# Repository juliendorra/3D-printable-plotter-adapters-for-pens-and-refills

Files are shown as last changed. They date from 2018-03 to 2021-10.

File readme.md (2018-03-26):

# 3D printable plotter adapters for pens and refills

Use your favorite contemporary pens on vintage HP plotters with this parametric OpenSCAD code to create custom adapters.

These adapters allow you to use pens or even directly refills with vintage HP plotters like the HP 7440A, HP 7550A, HP 7475A… and other vintage plotters using the same standard for pens.

This version was created to be quick and simple: **3 measures using a caliper, and in 5 minutes you are ready to print a new adapter** (printing itself will take maximum 20 minutes, depending on your settings and printer).

The goal was to be able to create an adapter for any random pen laying around or newly bought without thinking to much about it, trying and see what works best.

If you are interested in vintage plotters but don't know where to start, here's a list of ressources, manuals, articles, posts and artworks: [https://workflowy.com/s/Cl4.I8zutkIg5K](https://workflowy.com/s/Cl4.I8zutkIg5K)

You can also check the [#plottertwitter hashtag on Twitter](https://twitter.com/hashtag/plottertwitter).

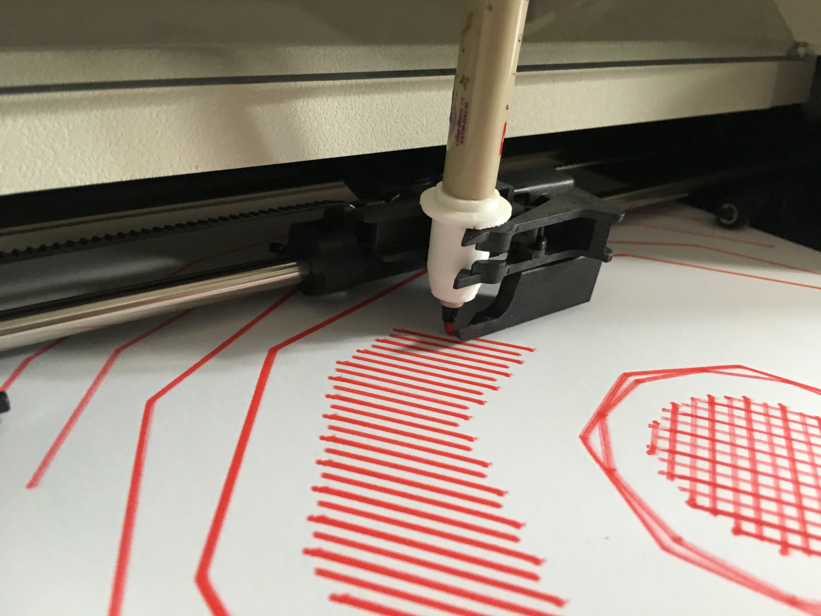
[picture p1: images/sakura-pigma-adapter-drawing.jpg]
sakura-pigma-adapter-drawing

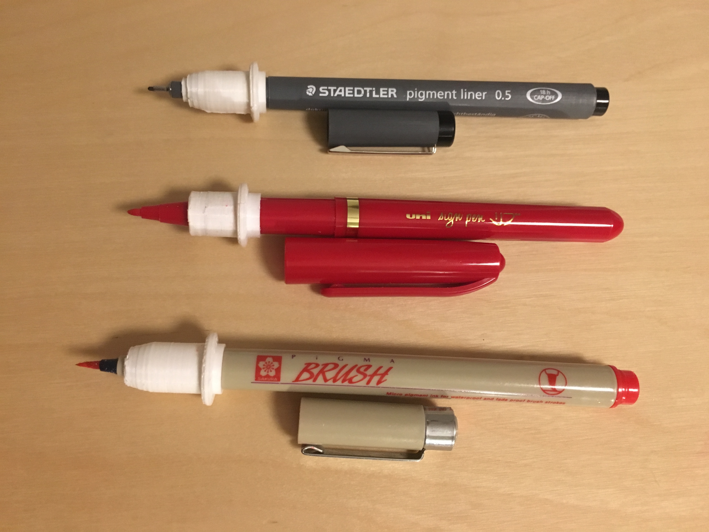
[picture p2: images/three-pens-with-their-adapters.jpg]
three-pens-with-their-adapters


## How to create your own adapter to use your favorite pen on your vintage HP plotter:

- Duplicate one of the existing OpenSCAD adapter files, for example `Staedtler pigment line plotter pen adapter.scad` (note that you'll need to keep the `plotter_pen_adapters_common.scad` file in the same folder as your new file, as it is imported by your adapter code)

- Select a stop-point near the tip of your pen. It is frequently the cap limit, but sometimes it more practical to use another narrowing along the body of the pen.

- Measure the maximum diameter of your pen above and below the chosen stop point, and add them to the `pen_top_diameter` (bigger) and `pen_bottom_diameter` (smaller) parameters.

- Measure the distance from the tip (ie. the paper) to the stop-point, and add that value to `height_where_pen_diameter_change`.

Note: for proper measuring, it is easier and more precise to use a caliper.

Optionnally, you can also adjust :

- `diameter_spacing` Increase to have lower tolerances (more space) and make it easier to slide the pen in and out. Decrease to have higher tolerances (less space) and have a tigher fit for the pen.

- `top_cut_off_height` It can reasonably be adjusted between `total_body_height - 11.5` and `total_body_height - 0` (Full height of the top body. Longer printing time). If you cut below `total_body_height - 11.5` the grip might suffer (to be tested :-)

- `simplified_body_shape` By default, the generator uses a realistic body shape for the adapter outer body, similar to the original HP pens. Add `simplified_body_shape = true ;` to your adapter code to use a simplified cylindrical lower body.  
You **will need** to use the simplified lower body if the `height_where_pen_diameter_change` value for your stop point is low, close to the paper as with the Edding calligraphy pens, and/or if the `pen_bottom_diameter` value is high, the pen being wide at the tip. In this cases the realistic body is not wide enough to allow for substracting the lower cylinder, cutting the adapter short or creating a hole in it.  
The downside of using the simplified body is that the adapter will no longer fit in a pen plotter rack or carrousel.

## 3D Printing

The printing shouldn't take more than 20 minutes, maybe less with a better printer that the low-cost (300€!) printer that was used to print the first adapters.

The main obstacle to properly printing these adapters is the flange (or band) around the adapter's body, which overhang.

You might very well be able to print it without support, but the first test were nicely successful by using the supports generated by Slic3r Prusa Edition (**not** on an Original Prusa i3). The supports were easy to remove, didn't add too much time and helped get a functionnal print.

You can use a very low infill. The first adapters were printed with a 10% cubic infill and are strong enough.

## This is based off:

- [Code from Sasha Kovar from a design by Brian Boucheron](https://www.thingiverse.com/thing:1261805/)
- [Code and measurements by Ed Nisley KE4ZNU April 2015](https://softsolder.com/2015/04/21/hp-7475a-plotter-oem-pen-body-model/) 

It differs and merge them in the following ways:

- the whole plotter HP pen model from Ed Nisley is used as a base. 
- then we substracts two cylinders. They are used as empty space for the target pen.
- The bottom cylinder is meant to be smaller than the top one, as most pens narrow before the tips.
-  The height where the pen diameter change is used as a parametric stop-point, set so the tip of the pen exactly touch the paper. 

It's also inspired by these other projects:

- [Full model of short and long plotter pens OpenSCAD file](https://www.thingiverse.com/thing:227985)

- [Ball pen insert adapter derived from the full models. STL file.](https://www.thingiverse.com/thing:762716)

## To do

- Emboss the reference or name of the pen around the pen adapter to avoid confusion when you have multiple adapters

- Add and test a tilt angle parameter to give a slight fixed angle to the tip when touching the paper. The maximum angle possible would need to be tested to avoid collisions. It might help in using highlighters or other asymetrical tips.

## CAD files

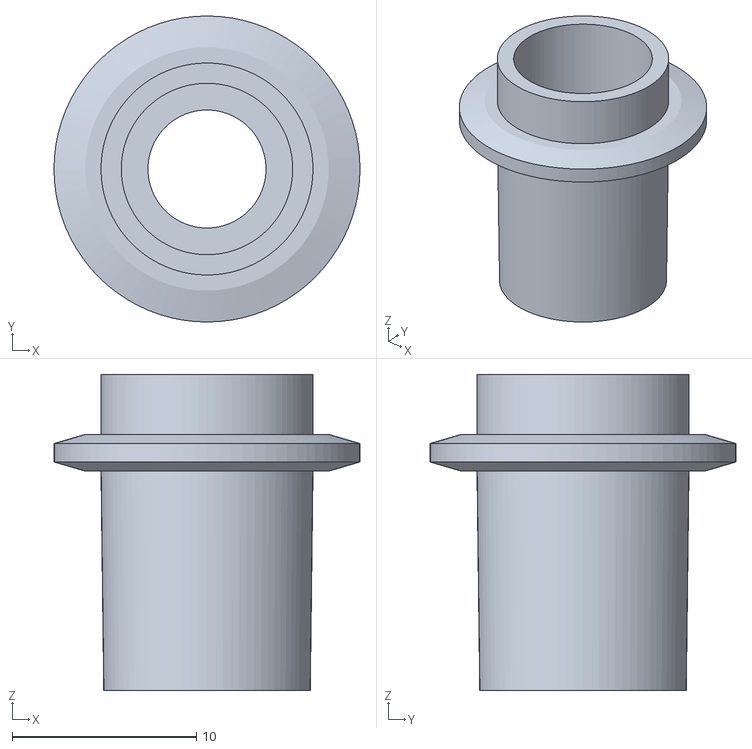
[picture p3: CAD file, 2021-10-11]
DeSerres Mateo plotter pen adapter.stl
16.6 x 16.6 x 17.2

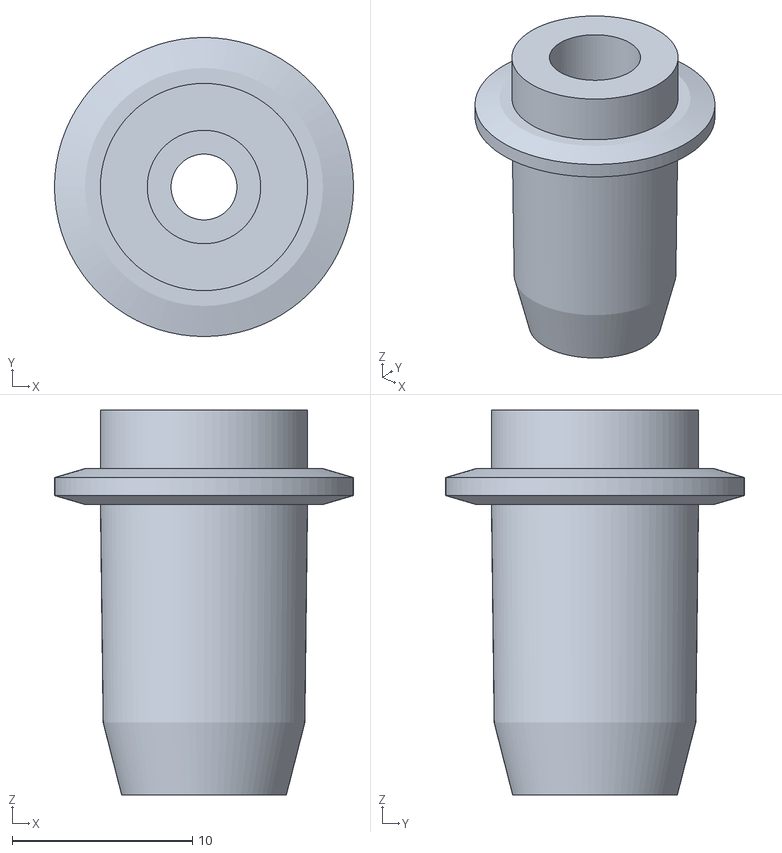
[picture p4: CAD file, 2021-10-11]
muji_pen_2021.stl
16.6 x 16.6 x 21.4

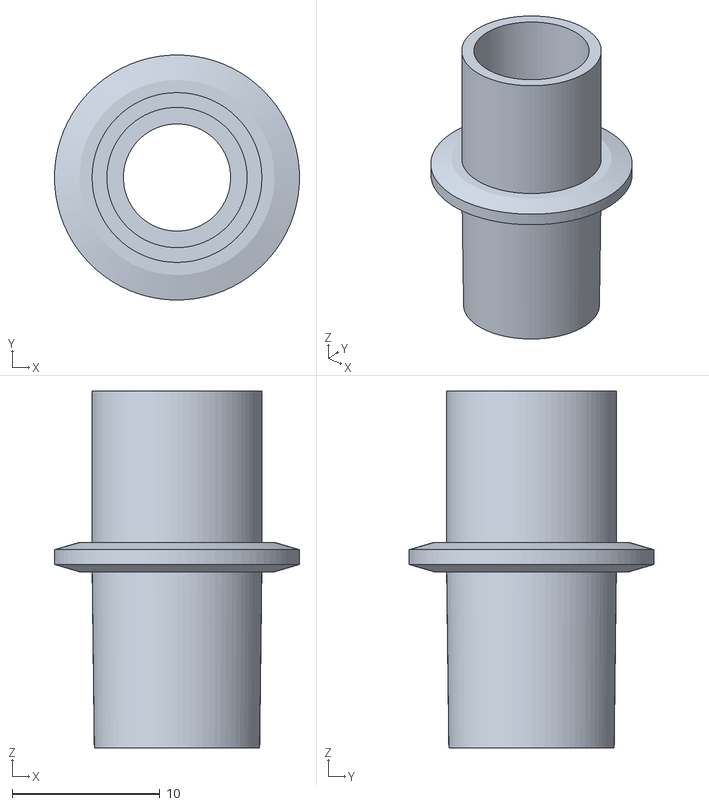
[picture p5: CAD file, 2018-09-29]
Sakura Koi coloring brush pen adapter.stl
16.6 x 16.6 x 24.2

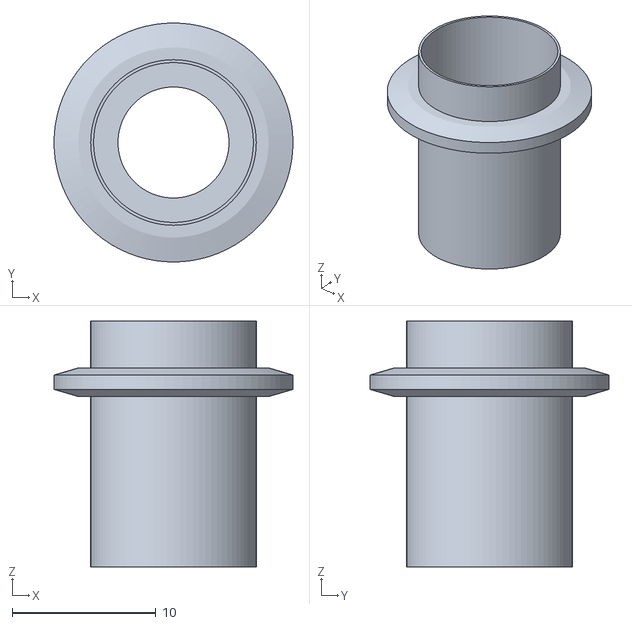
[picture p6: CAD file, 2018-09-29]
Kuretake Zig calligraphy pen adapter.stl
16.6 x 16.6 x 17.1

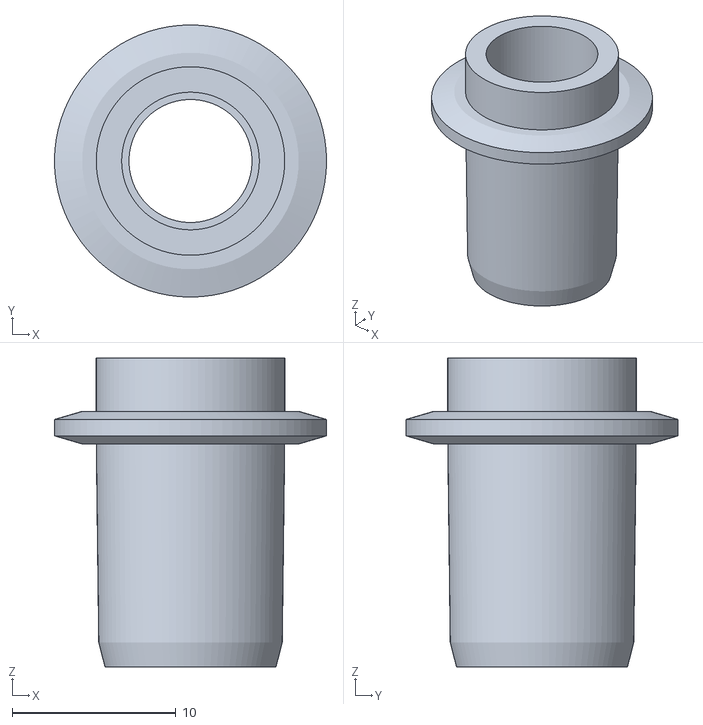
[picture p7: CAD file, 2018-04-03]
Pentel Slicci pen adapter.stl
16.6 x 16.6 x 18.9

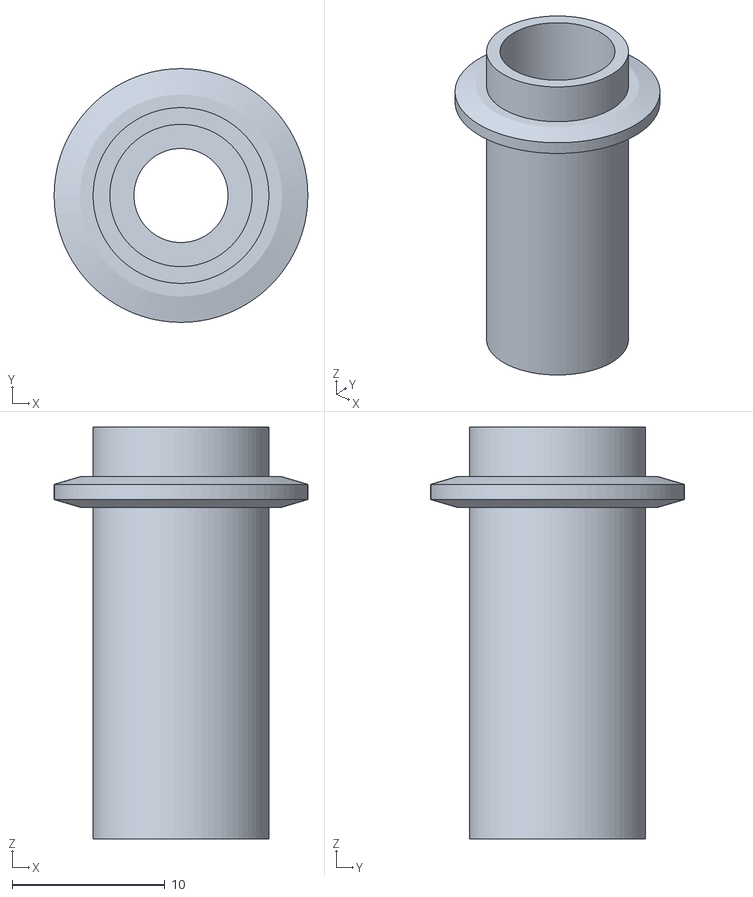
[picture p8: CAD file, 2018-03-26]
Edding 1255 calligraphy pen.stl
16.6 x 16.6 x 26.9

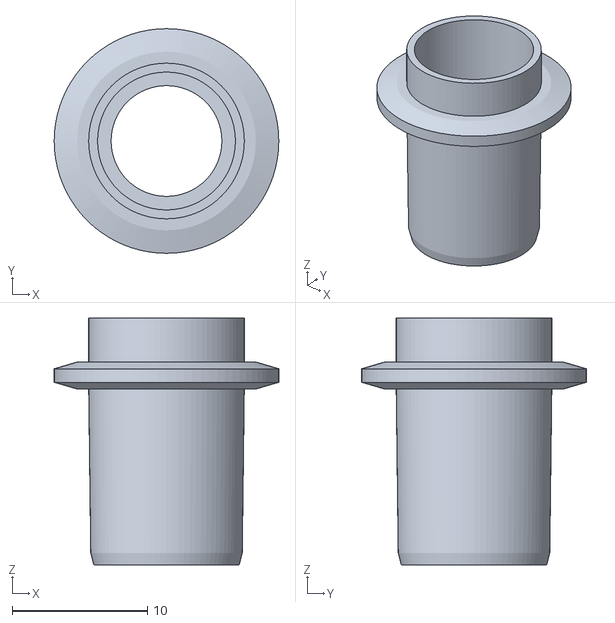
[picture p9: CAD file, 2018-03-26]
Pentel Arts brush pen adapter.stl
16.6 x 16.6 x 18.2

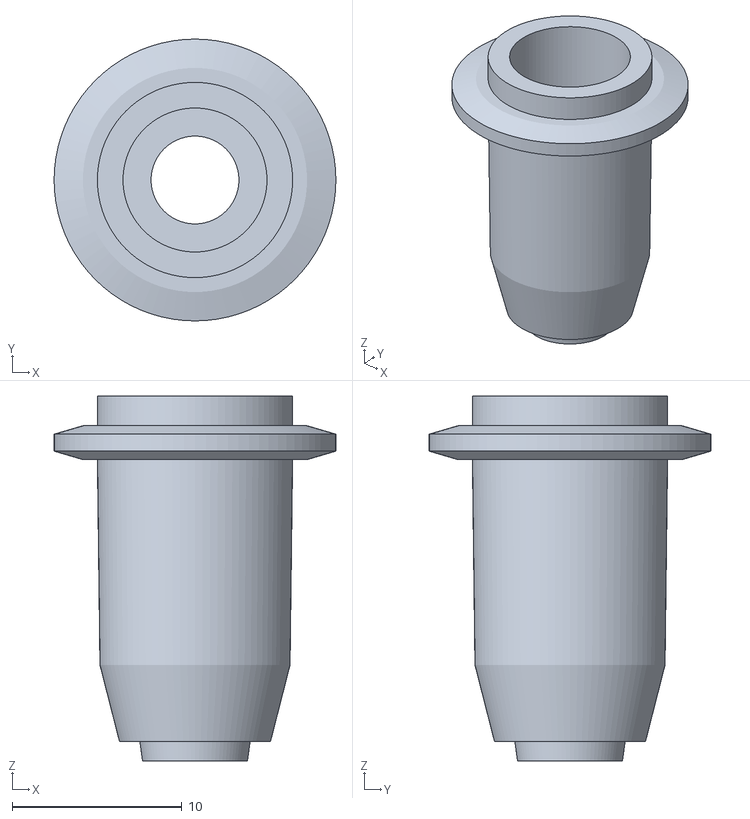
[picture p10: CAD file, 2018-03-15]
Sakura Pigma brush adapter.stl
16.6 x 16.6 x 21.5

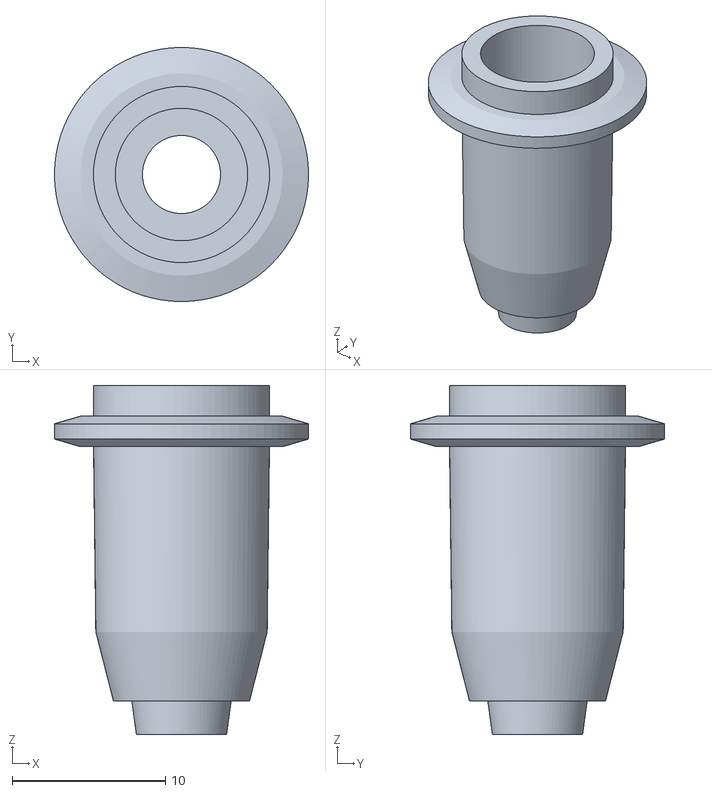
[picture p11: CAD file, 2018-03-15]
Staedtler pigment line plotter pen adapter.stl
16.6 x 16.6 x 22.8

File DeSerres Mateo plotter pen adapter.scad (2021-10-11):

// DeSerres 1.0mm Mateo Marker 
// https://www.deserres.ca/products/1-0mm-mateo-marker
// Plotter pen adapter - scruss, 2021-08
// (very similar to Stabilo point 88)

include <plotter_pen_adapters_common.scad>;
 
pen_top_diameter = 9.0;
pen_bottom_diameter = 6.1; 

diameter_spacing = 0.3 ; // increase = easier to slide the pen. If you set it to 0 it will be very hard to get the pen in.

height_where_pen_diameter_change = 19.1; // Measured from the tip (ie. paper)

bottom_cut_off_height = height_where_pen_diameter_change - 3 ; 

top_cut_off_height = total_body_height - 10 ;


adapter_minus_pen() ;

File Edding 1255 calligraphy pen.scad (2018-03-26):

// Edding 1255 calligraphy pen
// Plotter pen adapter

include <plotter_pen_adapters_common.scad>;
 
pen_top_diameter = 9.01 ; 
pen_bottom_diameter = 5.85 ; 

diameter_spacing = 0.3 ; // increase = easier to slide the pen. If you set it to 0 it will be very hard to get the pen in.

height_where_pen_diameter_change = 9.30 ; // Measured from the tip (ie. paper)

bottom_cut_off_height = height_where_pen_diameter_change - 3 ; 

top_cut_off_height = total_body_height - 10 ; 

simplified_body_shape = true ; // we need the simplified body because the real body is too thin at the bottom, and this adapter need to go nearly all the way down to the tip 

adapter_minus_pen() ;

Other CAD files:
Uni-ball Signo broad pen adapter.stl
Uni-ball Signo fine pen adapter.stl
Stabilo point 88 plotter pen adapter.stl
Uni Sign pen.stl
muji color gel pen refill adapter.stl
muji gel pen refill adapter.stl
Kuretake Zig calligraphy pen adapter.scad
muji color gel pen refill adapter.scad
Pentel Arts brush pen adapter.scad
Pentel Slicci pen adapter.scad
Sakura Koi coloring brush pen adapter.scad
Sakura Pigma brush adapter.scad
Stabilo point 88 plotter pen adapter.scad
Staedtler pigment line plotter pen adapter.scad
Uni Sign pen.scad
Uni-ball Signo broad pen adapter.scad
Uni-ball Signo fine pen adapter.scad
muji_pen_2021.scad
plotter_pen_adapters_common.scad

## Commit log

2018-03-13 multiple possibilities
    [muji black 0.5 adapter.scad, muji gel pen refill adapter.scad, muji gel pen refill adapter.stl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]
2018-03-13 body_height, more facets
    [plotter_pen_adapters_common.scad]
2018-03-13 proper top cut, credits for the plotter pen body
    [muji gel pen refill adapter.scad]
2018-03-13 updated version from new code
    [muji gel pen refill adapter.stl]
2018-03-13 comparing the two plotter pens
    [plotter_pen.scad]
2018-03-14 updates on pens and dimensions
    [Staedtler pigment line plotter pen adapter.scad, muji black 0.5 adapter.scad, muji color gel pen refill adapter.scad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]
2018-03-14 call module instead of duplicating it
    [Staedtler pigment line plotter pen adapter.scad]
2018-03-15 Two new pen adapters
    [Sakura Pigma brush adapter.scad, Sakura Pigma brush adapter.stl, Uni Sign pen.scad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]
2018-03-19 Add Stabile point 88 adapter
    [Stabilo point 88 plotter pen adapter.scad, Stabilo point 88 plotter pen adapter.stl]
2018-03-26 Pentel Arts brush and Uni-ball Signo fine adapters
    [Pentel Arts brush pen adapter.scad, Pentel Arts brush pen adapter.stl, Uni-ball Signo fine pen adapter.scad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]
2018-03-26 Alternative simplified adapter body for stop points too close to tip
    [plotter_pen_adapters_common.scad]
2018-03-26 Edding 1255 calligraphy pens with simplified body
    [Edding 1255 calligraphy pen.scad, Edding 1255 calligraphy pen.stl]
2018-04-03 New pen adapters (Slicci, Signo broad)
    [Pentel Slicci pen adapter.scad, Pentel Slicci pen adapter.stl, Uni-ball Signo broad pen adapter.scad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]
2018-09-29 Kuretake Zig
    The Kuretake Zig diameter similar to the diameter of the original HP
    plotter pens, and thus it is needed to cut this adapter along its body
    for the pen to fit. Not ideal.
    [Kuretake Zig calligraphy pen adapter.scad, Kuretake Zig calligraphy pen adapter.stl]
2018-09-29 Sakura Koi adapters
    [Sakura Koi coloring brush pen adapter.scad, Sakura Koi coloring brush pen adapter.stl]
2021-08-23 added DeSerres Mateo marker adapter
    these are a cheaper, wider near-clone of the Point 88.
    Product link: [DeSerres 1.0mm Mateo Marker](https://www.deserres.ca/products/1-0mm-mateo-marker)
    [DeSerres Mateo plotter pen adapter.scad, DeSerres Mateo plotter pen adapter.stl]
2021-08-24 muji 2021 edits
    [muji_pen_2021.scad, muji_pen_2021.stl]
